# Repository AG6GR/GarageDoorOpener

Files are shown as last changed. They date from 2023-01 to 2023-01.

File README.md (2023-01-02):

# Garage Door Opener

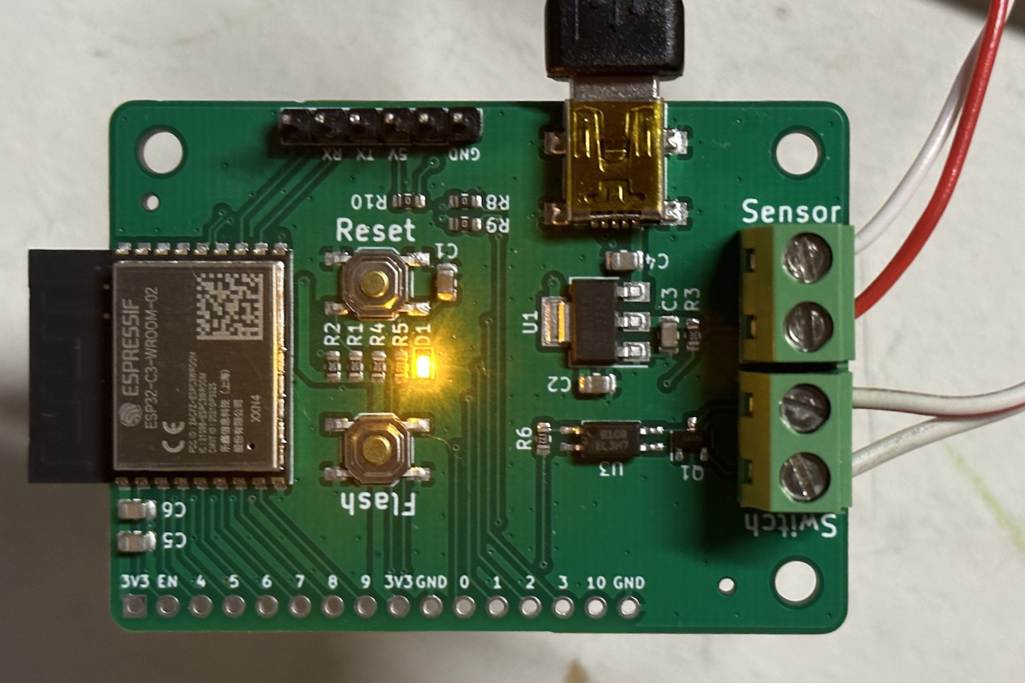
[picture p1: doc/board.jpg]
Finished PCB


A bare-bones ESP32 based HomeKit enabled garage door opener using [HomeSpan](https://github.com/HomeSpan/HomeSpan).

# Hardware

To avoid any modification to the garage door opener itself, I designed the board to use its own position sensor and emulate a wall switch to trigger the garage door movement. Some commercial products emulate a wireless remote and indeed the ESP32 does have some [special function hardware](https://github.com/HomeSpan/HomeSpan/blob/master/docs/RMT.md) for generating pulse code signals, however I decided to skip the complexity for this first revision as the holiday season presented some serious schedule pressure for getting this finished. Likewise, for the door position sensor some products use a tilt sensor with the assumption the board would be glued to the moving door itself. I again opted for the simpler solution of a microswitch mounted on one of the door's guide rails to avoid the complexity of dealing with battery power and wireless control.

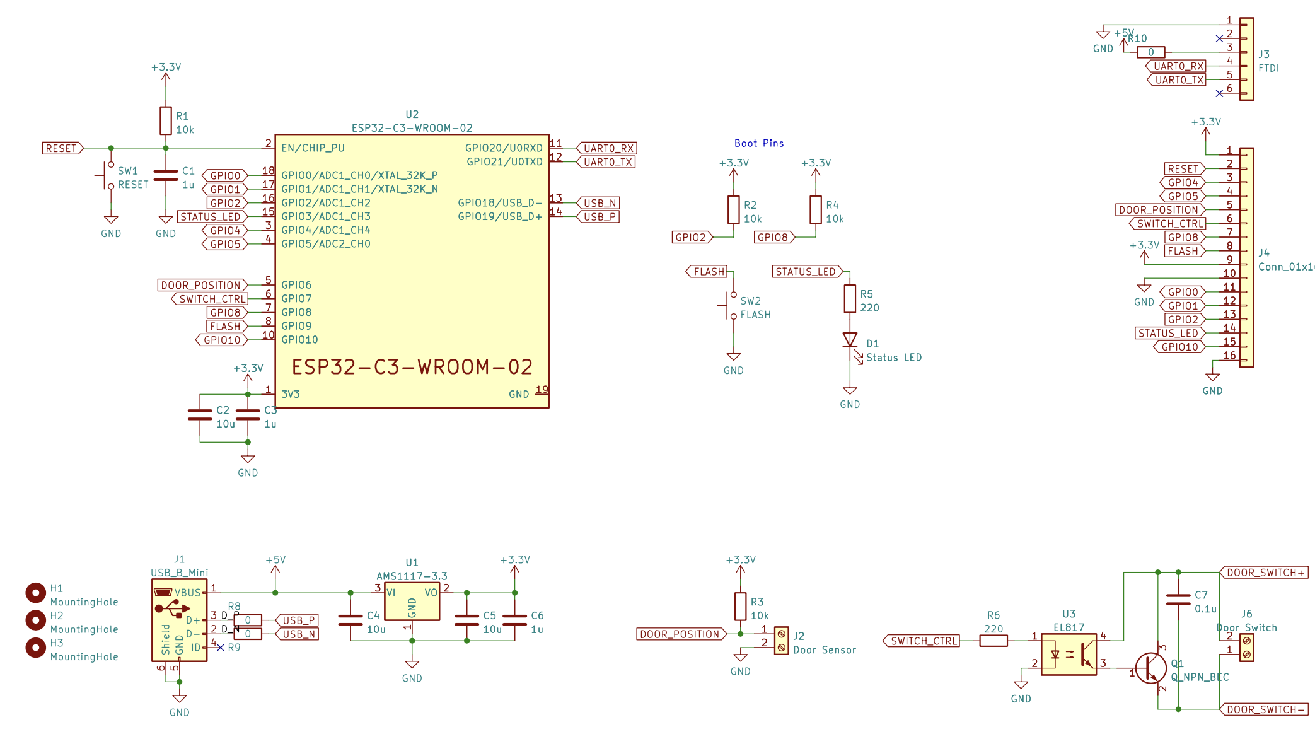
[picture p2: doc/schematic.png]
Schematic


To actuate the door, a wall switch normally would short a pair of lines connected to terminals on the back of the garage door opener. I measured these terminals with a voltmeter and found the high side was pulled up to 24V nominal, above some floating ground potential. Also of note is that the threshold voltage for triggering was quite low, less than 0.1V difference. The ideal part to use in this case would be a small relay, but I didn't have any on hand. As an alternative, I ended up using an optoisolator with an NPN transistor in a Darlington configuration to achieve the isolation and current capacity needed to drive the opener's trigger line low.

One unexpected issue that came up after the board arrived was that the NPN BJT was not fully turning on before the line voltage collapsed, leaving the line stuck at a ~0.7V base emitter diode voltage, which was just a bit above the threshold voltage for triggering the opener. I bodged in a 0.1 µF capacitor between the high/low side of the screw terminal to fix this. The extra capacitance ensures the BJT has just enough time to fully turn on, driving the line completely low and triggering the opener.

# Firmware

The firmware relies on the excellent [HomeSpan](https://github.com/HomeSpan/HomeSpan) project to implement HomeKit support. It was very straightforward to implement a GarageDoorOpener service and hook it up to the appropriate inputs/outputs. With some fine tuning of switch debouncing, everything was installed and ready by Christmas.

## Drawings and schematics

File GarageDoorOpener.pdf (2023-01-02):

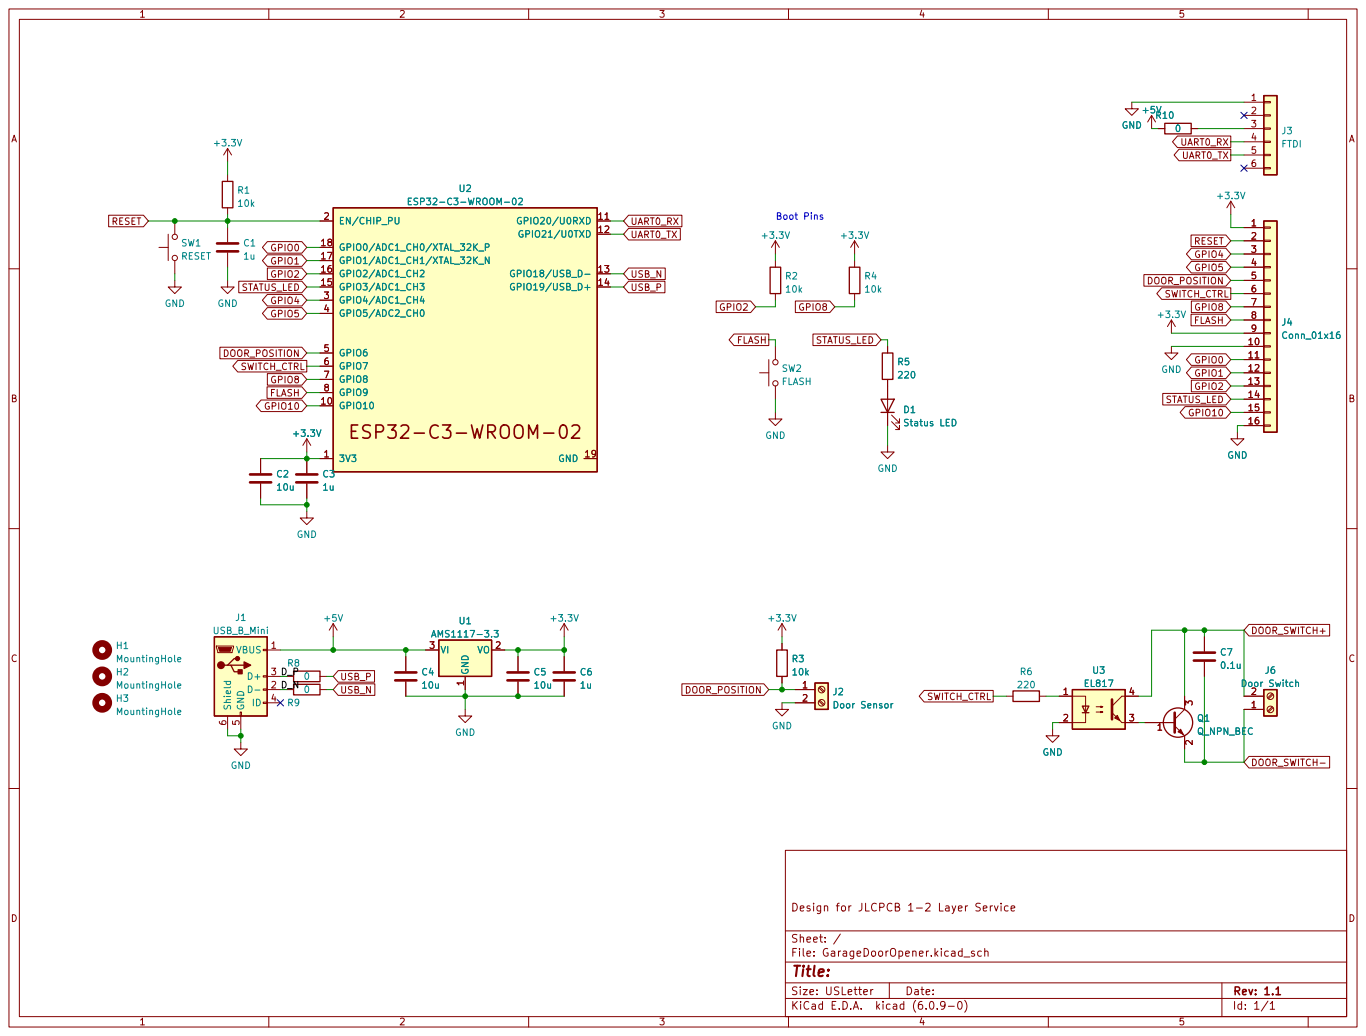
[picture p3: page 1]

File: GarageDoorOpener.kicad_sch Sheet: / Design for JLCPCB 1-2 Layer Service GND
J1 USB_B_Mini GND

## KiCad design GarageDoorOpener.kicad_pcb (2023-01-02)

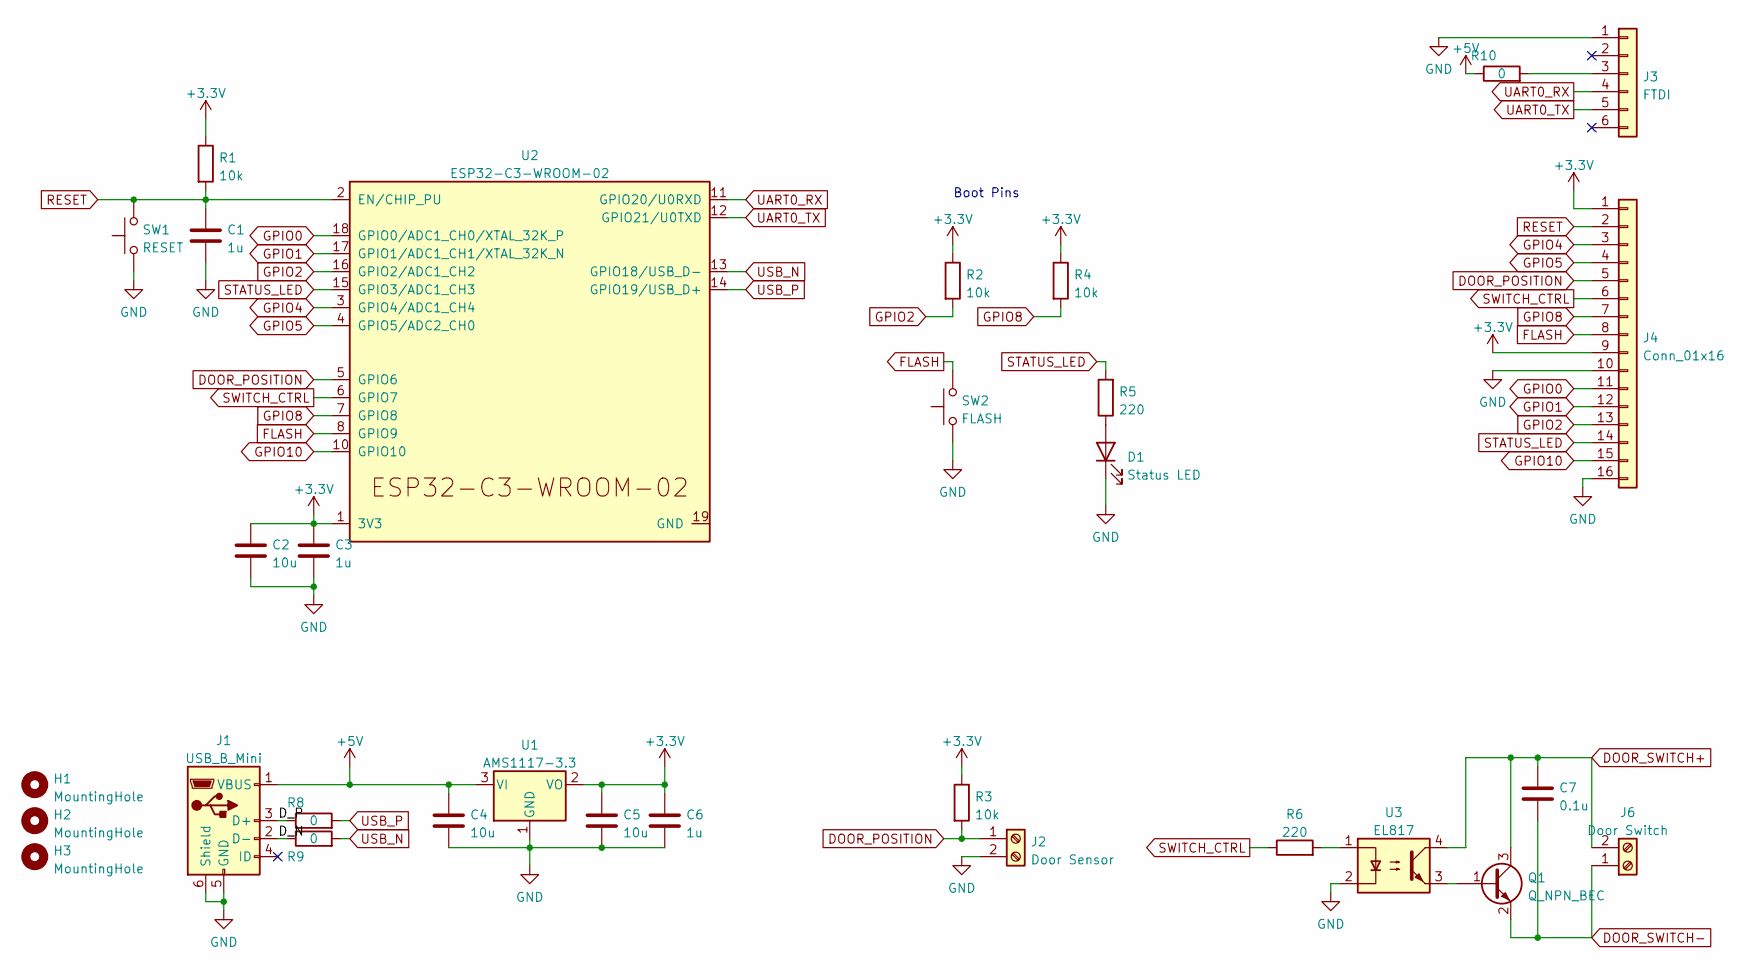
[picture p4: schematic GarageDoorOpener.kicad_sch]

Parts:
C1, C3, C6: 1u; C_0805_2012Metric
C2, C4, C5: 10u; C_0805_2012Metric
C7: 0.1u; C_0805_2012Metric
D1: Status LED; LED_0603_1608Metric
H1, H2, H3: MountingHole; MountingHole_3.2mm_M3
J1: USB_B_Mini; USB_Mini-B_Lumberg_2486_01_Horizontal
J2: Door Sensor; TerminalBlock_bornier-2_P5.08mm
J3: FTDI; PinHeader_1x06_P2.54mm_Vertical
J4: Conn_01x16; PinHeader_1x16_P2.54mm_Vertical
J6: Door Switch; TerminalBlock_bornier-2_P5.08mm
Q1: Q_NPN_BEC; SOT-23
R1, R2, R3, R4: 10k; R_0603_1608Metric
R5, R6: 220; R_0603_1608Metric
R8, R9, R10: 0; R_0603_1608Metric
SW1: RESET; SW_SPST_TL3342
SW2: FLASH; SW_SPST_TL3342
U1: AMS1117-3.3; SOT-223-3_TabPin2
U2: ESP32-C3-WROOM-02
U3: EL817; EL3H7

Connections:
+3.3V: C2.1, C3.1, C5.1, C6.1, J4.1, J4.9, R1.1, R2.1, R3.1, R4.1, U1.2 (VO), U2.1 (3V3)
+5V: C4.1, J1.1 (VBUS), R10.1, U1.3 (VI)
/D_N: J1.2 (D-), R9.1
/D_P: J1.3 (D+), R8.1
DOOR_POSITION: J2.1, J4.5, R3.2, U2.5 (GPIO6)
DOOR_SWITCH+: C7.1, J6.2, Q1.3 (C), U3.4
DOOR_SWITCH-: C7.2, J6.1, Q1.2 (E)
FLASH: J4.8, SW2.2, U2.8 (GPIO9)
GPIO0: J4.11, U2.18 (GPIO0/ADC1_CH0/XTAL_32K_P)
GPIO1: J4.12, U2.17 (GPIO1/ADC1_CH1/XTAL_32K_N)
GPIO2: J4.13, R2.2, U2.16 (GPIO2/ADC1_CH2)
GPIO4: J4.3, U2.3 (GPIO4/ADC1_CH4)
GPIO5: J4.4, U2.4 (GPIO5/ADC2_CH0)
GPIO8: J4.7, R4.2, U2.7 (GPIO8)
GPIO10: J4.15, U2.10 (GPIO10)
unnamed: D1.2 (A), R5.1
unnamed: J3.3, R10.2
unnamed: Q1.1 (B), U3.3
unnamed: R6.2, U3.1
RESET: C1.1, J4.2, R1.2, SW1.2, U2.2 (EN/CHIP_PU)
STATUS_LED: J4.14, R5.2, U2.15 (GPIO3/ADC1_CH3)
SWITCH_CTRL: J4.6, R6.1, U2.6 (GPIO7)
UART0_RX: J3.4, U2.11 (GPIO20/U0RXD)
UART0_TX: J3.5, U2.12 (GPIO21/U0TXD)
USB_N: R9.2, U2.13 (GPIO18/USB_D-)
USB_P: R8.2, U2.14 (GPIO19/USB_D+)

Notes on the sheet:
Boot Pins

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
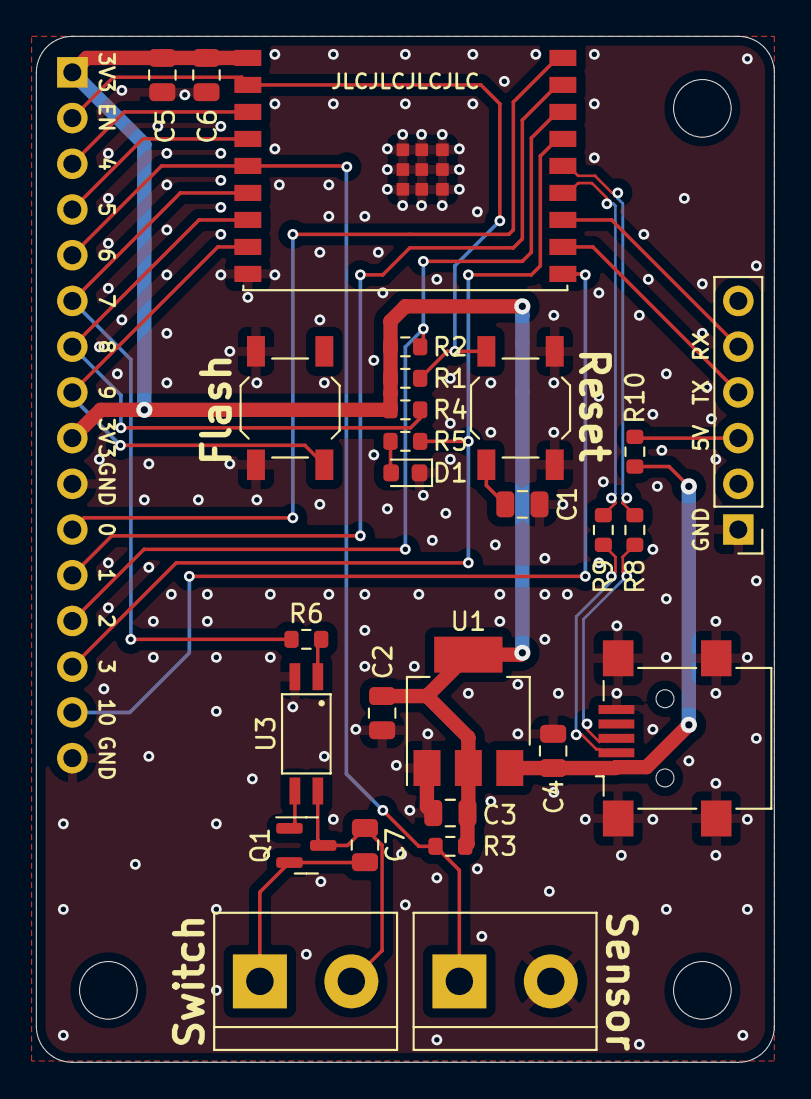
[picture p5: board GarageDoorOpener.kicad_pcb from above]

Board: 2 copper layers, 41.0 x 57.0 mm, 31 parts (0 on the bottom side), 27 nets.

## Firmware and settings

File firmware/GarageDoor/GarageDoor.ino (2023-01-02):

/*
 * (C) 2022 Sunny He
 */

#include "GarageDoor.hpp"

#define PIN_STATUS_LED 3
#define PIN_DOOR_POSITION 6
#define PIN_DOOR_SWITCH 7

void setup() {
  Serial.begin(115200);

  // HomeSpan setup
  homeSpan.setStatusPin(PIN_STATUS_LED);
  homeSpan.enableOTA();
  homeSpan.enableWebLog(64,"pool.ntp.org","America/Los_Angeles","weblog");
  homeSpan.begin(Category::GarageDoorOpeners,"Garage Door");
  new SpanAccessory();

  // Accessory Information Service
  new Service::AccessoryInformation();
  new Characteristic::Identify();
  new Characteristic::Model("ESP32 Dev Board");
  new Characteristic::FirmwareRevision("0.1"); 
  
  new GarageDoor(PIN_DOOR_POSITION, PIN_DOOR_SWITCH);
}

void loop() {
  // put your main code here, to run repeatedly:
  homeSpan.poll();
}

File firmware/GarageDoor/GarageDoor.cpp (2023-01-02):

/*
 * (C) 2022 Sunny He
 */

#include "GarageDoor.hpp"

GarageDoor::GarageDoor(int sensorPin, int switchPin) : Service::GarageDoorOpener() {
  current = new Characteristic::CurrentDoorState(DOOR_CLOSED);
  target = new Characteristic::TargetDoorState(DOOR_CLOSED);

  this->sensorPin = sensorPin;
  this->switchPin = switchPin;

  pinMode(sensorPin, INPUT);
  pinMode(switchPin, OUTPUT);
  digitalWrite(this->switchPin, LOW);
  WEBLOG("Creating GarageDoor"); 
}

void GarageDoor::pressSwitch() {
  WEBLOG("Enabling switchPin");
  digitalWrite(this->switchPin, HIGH);
  delay(500);
  WEBLOG("Disabling switchPin");
  digitalWrite(this->switchPin, LOW);
}

boolean GarageDoor::update() {
  WEBLOG("update to %d", target->getNewVal());
  if (current->getVal() == target->getNewVal())
    return true;
  
  switch (target->getNewVal()) {
    case DOOR_OPEN:
      this->pressSwitch();
      break;
    
    case DOOR_CLOSED:
      this->pressSwitch();
      break;

    default:
      break;
  }
  return true;
}

void GarageDoor::loop() {
  if (current->timeVal() > 10000) {
    int readPos = digitalRead(this->sensorPin);
    bool stateChanged = false;
    if (readPos == LOW) {
      if (current->getVal() != DOOR_CLOSED) {
        WEBLOG("Detected door closed");
        current->setVal(DOOR_CLOSED);
        stateChanged = true;
      }
    } else {
      if (current->getVal() != DOOR_OPEN) {
        WEBLOG("Detected door open");
        current->setVal(DOOR_OPEN);
        stateChanged = true;
      }
    }

    if (stateChanged && target->timeVal() > 30000) {
      WEBLOG("No recent Homekit update of target state, set target = current");
      target->setVal(current->getVal());
    }
  }
}

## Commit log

2022-12-14 Board rev 1.0
    [GarageDoorOpener.kicad_pcb, GarageDoorOpener.kicad_sch, GarageDoorOpener.sch]
2022-12-15 Add schematic
2022-12-15 Add status LED pin
2022-12-19 Remove LED test
2022-12-19 Improve handling of external triggers and switch debouncing
2023-01-02 Add README
    [GarageDoorOpener.sch]
2023-01-02 Board rev 1.1, add switch capacitor
    [GarageDoorOpener.kicad_pcb, GarageDoorOpener.kicad_sch]
